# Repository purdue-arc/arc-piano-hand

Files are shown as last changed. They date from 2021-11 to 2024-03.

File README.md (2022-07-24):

---
title: Piano Hand - Overview
date: 2020-09-28 00:00:00 Z
author: Revanth Senthil
---

# Piano Hand - Purdue ARC

## Goal

<u>

### Mission

</u>

The primary objective of Piano Hand is to explore the perspective of robotics in replicating human-motion. Fascination for this included looking at tasks that would help us understand biomechanics, which is an area of robotics that has gained a lot of traction recently. 

The goal of the project is to build a fully autonomous robot arm that can play the piano. The human hand, with 27 degrees of freedom (DOF), has so far been the most dextrous mechanism to play the piano and the closer we get to replicating that degree of freedom and movement, the better it is to move the arm and play the piano.

{% include googleDrivePlayer.html id="1P8rwWDJa1Yuv88X697RMvEq04j1IgpqW/preview" %}

This semester (Fall 2022), we are planning to refine our working model of the animatronic hand built last semester with the help of accurate servo motor and flex sensor functioning. We would expect to extend functioning to two hands as well. Additionally, we are starting a new path in software along the lines of machine learning and optical image recognition by building a model that can read sheet music, given an image format.

---

## Repository Guide

The `Code` directory of this repository contains the software team's work in this project, and the `Models` directory consists of that of the hardware team. The sub-directories in these are divided based on the semester of progress. If any of the directories are incomplete, they will be updated soon. The `wiki` directory contains pretty much the same content as this file, and will be that you see on the wiki page of this project on the <a href="https://wiki.purduearc.com/">Club's Wiki</a>.

---

## What we have done

<u>

### Summer 2022

</u>

Ideated and designed new mechanisms for the hand that involves the usage of linear actuators and bevel gears. This design will be assembled and tested in Fall 2022 as a new iteration from the hand design in Spring 2022.

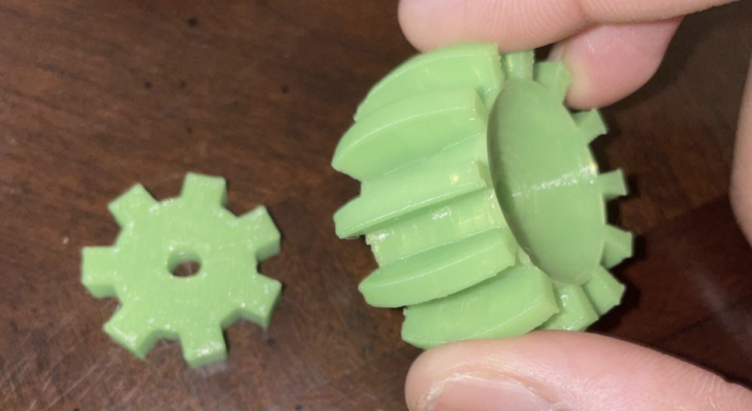
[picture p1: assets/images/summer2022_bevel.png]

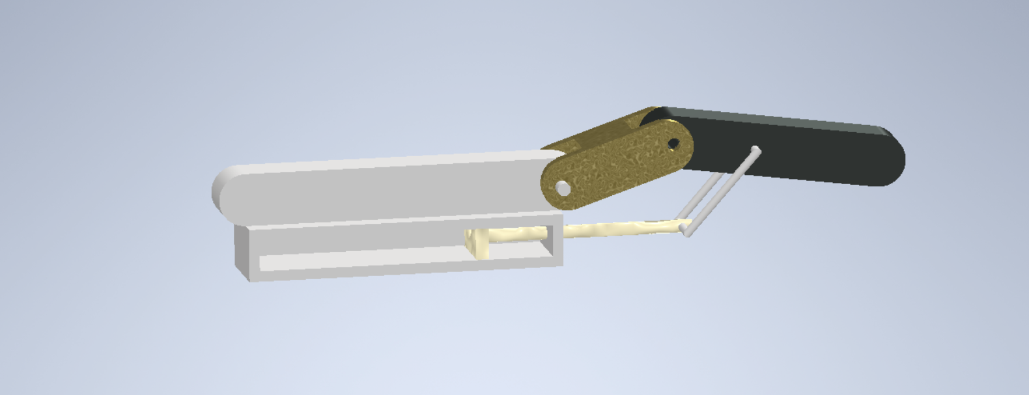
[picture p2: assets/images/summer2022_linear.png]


Worked on fixing issues that came about in software in Spring 2022, and in getting ready the design to implement on the hand in Fall 2023. Introduced new course of action alongside software to start with machine learning and model development in Optical Music Recognition.

Clip from working of servos:

{% include googleDrivePlayer.html id="12XIlDrckEdbvJNI8A9Jp3um2TsCtu46J/view" %}

<u>

### Spring 2022

</u>

Spring2022_Design

Worked on improving model developed in Fall 2021 by printing and testing. An add-on for attaching the servo motors was developed and the design was 3D-printed.

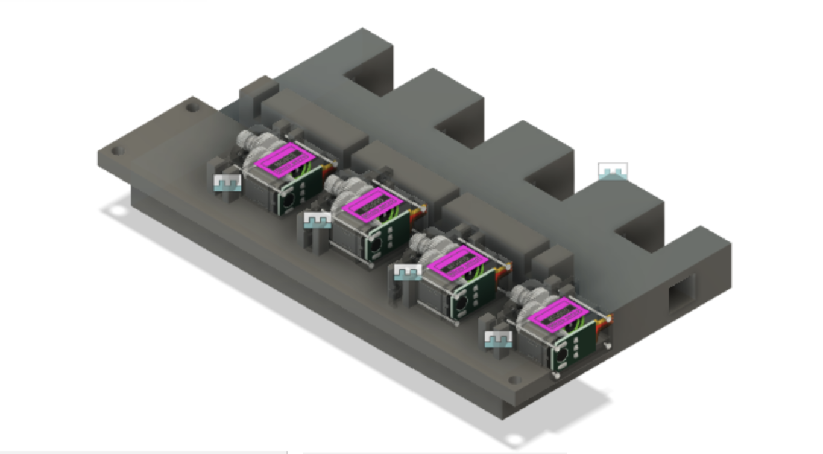
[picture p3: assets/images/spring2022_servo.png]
Spring2022_ServoAttach


Software work primarily included setup of environment on Arudino/Raspberry Pi, along with flex sensors. Issues with the usage of continuous servos were addressed. 8-bit ADCs were also used to improve testing.

{% include googleDrivePlayer.html id="1XUN3-VXOXNSEd7ECZbARMhXspTH0es3h/view" %}

<u>

### Fall 2021

</u>

Worked primarily on developing models and getting an idea of the different parts necessary to 3-D print. Produced the following first iteration of the hand by the end of the semester from hardware.

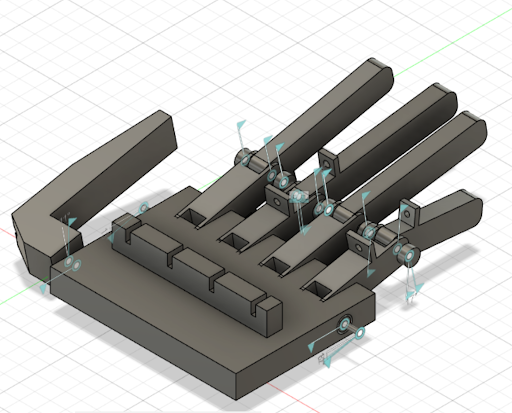
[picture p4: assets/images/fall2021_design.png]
Fall2021_Design


Software primarily worked on simulation and testing, and the following simulation was produced on TinkerCAD (TinkerCAD's electronic component simulator had Arduino testing capabilities and hence was useful for the first stage of testing). TInkerCAD's use-cases for simulation testing were visible from early testing with the software for multiple fingers, using MG90S servos.

{% include googleDrivePlayer.html id="1FLBJuV58_8QRsNKVJZqaC88cPaUbHi6O/view" %}

---

### Subteams and Roster

<u>

#### Project Manager

</u>

Revanth Krishna Senthilkumaran, Computer Engineering

<u>

#### Hardware

</u>

Hardware primarily works on making and refining CAD models with tools available, 3D printing models, assembling, testing and identifying points of improvement in the model and testing functionality. 

<ul>
<li>
<b>Lead</b>: Rugved Dikay, Aeronautical and Aerospace Engineering
</li>
<li>
Akshay, Electrical Engineering
</li>
<li>
Archis Behere, Mechanical Engineering
</li>
</ul>

<u>

#### Software

</u>

Software primarily works on developing the code and algorithms for the movement of the hand to locations computed, along with setup of the electrical systems. More recent initiatives include model development for optical music recognition and Raspberry Pi conversion from Arduino.

<ul>
<li>
Dhruv Sujatha, Data Science
</li>
<li>
Jacob Aldridge, Computer Science
</li>
<li>
Manas Paranjape, Computer Science
</li>
<li>
Visuwanaath Selvam, Computer Engineering
</li>
</ul>

---

<!-- ### Images/GIFs -->

<!-- ## Summary -->

## See Also:

<h3> Inspiration / Other Projects </h3>

<ol>

<li>
 A team of researchers attempted replicating the pressure applied in the grasping mechanism and achieved 17 DOF in a 5-finger hand. The actuators used are the most interesting: McKibben Actuators, which move on the basis of difference in Air Pressure. <a href="https://www.sciencedirect.com/science/article/pii/B9780081005743000102"> ScienceDirect article </a> 
</li>

<li>
The ILDA Robot Hand: A 15 DOF, highly tactile robot hand, motion along surface of palm, and stepper motor actuation. Some of its capabilities include crushing cans, delicate grasping, and tactile tasks such as tapping. <a href="https://gizmodo.com/lifelike-robotic-hand-is-a-bit-too-close-to-terminator-1848213189"> Overview and Videos of Functioning </a> |  <a href="https://www.nature.com/articles/s41467-021-27261-0"> Nature article </a>
</li>

<li>
Soft actuated robots - <a href="https://dash.harvard.edu/bitstream/handle/1/25922120/66841469.pdf;sequence=1"> Harvard paper </a> | 
</li>

<li>
WPI - <a href="https://web.wpi.edu/Pubs/E-project/Available/E-project-042919-161531/unrestricted/Piano_Playing_Robotic_Arm_MQP_-_Final.pdf"> MQP
</li>

<li>
Allegro Hand - <a href="http://wiki.ros.org/Robots/AllegroHand">ROS Documentation</a> | <a href="https://www.youtube.com/watch?v=WzJJ4c6AqnE"> MIT Grad Student's Piano Hand</a>
</li>

<li>
Robot Nano Hand - <a href="https://youtu.be/uOeS_jklU2Y">YouTube</a> | <a href="https://robotnanohand.com/"> Site </a> 
</li>

<li>
InMoov Robot Hand - <a href="https://www.thingiverse.com/thing:17773">Parts and Paper Link</a>
</li>

<li>
Other similar project resources: <a href="https://create.arduino.cc/projecthub/laurencemlai/diy-glove-controlled-robotic-hand-ff5d63"> Arduino Project Hub </a> | <a href="https://www.instructables.com/DIY-Robotic-Hand-Controlled-by-a-Glove-and-Arduino/"> Instructables </a>
</li>

<li>
Video Links/Pages referred: <a href="https://www.youtube.com/c/WillCogley">Will Cogley</a> | Automation Robotics' <a href="https://www.youtube.com/channel/UCd0xLOw6No5IAsq3Y2-b0eA">Clone</a>
</li>

</ol>

<h3> References </h3>

<ol>

<li>
Piano Keys Research - <a href="https://music.stackexchange.com/questions/53847/what-are-the-dimensions-of-piano-keys-in-inches"> Dimensions </a>
</li>

<li>
Joint Design - <a href="https://www.youtube.com/watch?v=AJ9zVYQw5XU">Ball and Socket</a> 
</li>

<li>
Optical Music Recognition Datasets - <a href="https://apacha.github.io/OMR-Datasets/"> Apacha Database List </a> | <a href="https://tuggeluk.github.io/deepscores/"> Deepscores </a> | <a href="https://grfia.dlsi.ua.es/primus/"> Primus </a>
</li>

<li>
Raspberry Pi-Arduino Connectivity - <a href="https://www.aranacorp.com/en/communication-between-raspberry-pi-and-arduino-with-i2c/"> AranaCorp </a> | <a href="https://maker.pro/raspberry-pi/tutorial/raspberry-pi-4-gpio-pinout"> Pi4 GPIO </a> 
</li>

<li>
Parts - <a href="https://cdn-learn.adafruit.com/downloads/pdf/adafruit-4-channel-adc-breakouts.pdf">ADCs</a> | Multi-channel Servo Controller (<a href="https://www.adafruit.com/product/2327?gclid=COGwqIfL99ECFYQDaQodjtQPXQ">16</a>, <a href="https://shop.pimoroni.com/products/servo-2040?variant=39800591679571">18</a>) | <a href="https://www.youtube.com/watch?v=2vAoOYF3m8U"> Linear Servo Actuators </a> - <a href="https://www.myminifactory.com/object/3d-print-77542">CAD Files 1</a>, <a href="https://www.thingiverse.com/thing:3170748/files">CAD Files 2</a>
</li>

<li>
Add-ons: Strings/Thread <a href="https://www.amazon.com/Cotton-String-Cooking-Kitchen-Wrapping/dp/B07KVSVTVV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"> 1 </a>, <a href="https://www.amazon.com/gp/product/B01FICZLU8/ref=ewc_pr_img_2?smid=A27A1UMDQYE0QB&th=1"> 2 </a> | <a href="https://www.amazon.com/Winter-Gloves-Men-Women-Waterproof/dp/B09FPS6HHH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"> Gloves </a>
</li>

<li>
DOF Analysis - <a href="https://www.researchgate.net/publication/264907843_Real-time_hand_tracking_for_rehabilitation_and_character_animation"> +Real-time Hand Tracking </a> | <a href="https://support.ptc.com/help/creo/creo_pma/r6.0/usascii/index.html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">Calculator</a> | <a href="https://www.mecharithm.com/degrees-of-freedom-of-a-robot/"> Mecharithm </a> | <a href="https://www.techopedia.com/definition/12702/six-degrees-of-freedom-6dof"> Technopedia </a>
</li>

<li>
Interesting Actuation Methods - <a href="https://www.frontiersin.org/articles/10.3389/frobt.2020.586216/full">Voltage-Controlled Linear Actuation</a>
</li>

</ol>

<!-- ## References -->

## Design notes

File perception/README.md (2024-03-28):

## Installation
* Install Dependencies (cv2, subprocess,skimage,numpy,imutils)
* Update filepaths (lines 204-206 in camScannerAuto.py)
* Run camScannerAuto.py

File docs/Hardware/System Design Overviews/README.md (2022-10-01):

This folder is to be used to store any documentation developed regarding the different actuation systems researched and modeled
during the design process for Piano Hand. Ultimately these documents/report will serve as the foundation for a comprehensive project
report, while currently demonstrating the thoughts behind engineering decisions, and to guide continous hand improvement.

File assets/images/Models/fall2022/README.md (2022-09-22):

This folder contains all the CAD files for the new designs developed for the Piano Hand during the Fall 2022 Academic semester. In total, 2 different prototype hands were developed: 
One uses geared finger actuation and geared finger seperation, and the other uses linear actuators for actuation, along with a similar geared finger seperation.

All these CAD files have been uploaded in their .f3d formats, or that naturally compatible with Fusion 360 software for easy download and upload. STL conversions
will be provided towards the end of the semester for more general use.

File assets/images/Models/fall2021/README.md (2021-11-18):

# CAD Models for the Piano Hand

### Hardware team of Piano Hand to upload CAD Models of the Hand and its progress throughout the semester, including the ProtoHand

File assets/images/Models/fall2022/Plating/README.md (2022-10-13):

This folder will serve as a repository for all CAD files related to supporting elements of the Piano Hand design. Primarily this refers to the plating that shall
surround the different components, gears, and joints of the hand as well as any connecting parts between these plates and the internal elements.

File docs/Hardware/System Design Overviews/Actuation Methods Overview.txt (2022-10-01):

After reviewing different finger actuation systems such as using gears, cables, and linear actuators as well as creating a prototype based on the cable method last semester, linear actuation will be the focus this semester. The cable based method turned out to be unreliable to control and code for finer motion. Due to the results from testing the cable method, linear actuators seem to be a better alternative both in regards to precision and most imporantly in size. Though right now the focus is on linear actuators, gear-based systems are also one alternative we are considering possibly in combination to linear actuators.

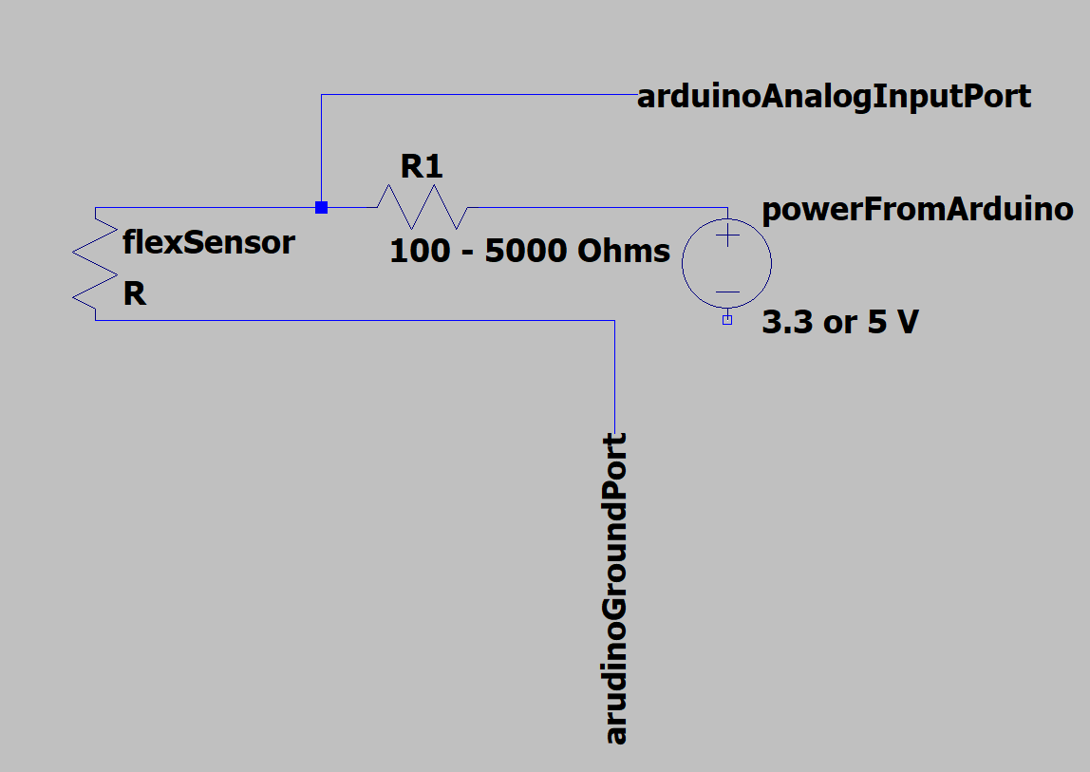
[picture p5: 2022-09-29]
src/code_timeline/fall2022/flexSensorCircuit.png

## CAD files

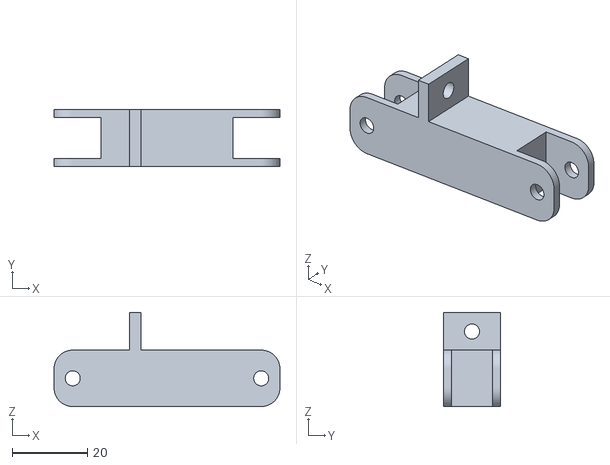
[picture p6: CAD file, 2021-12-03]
assets/images/Models/fall2021/Main_Finger_Joint.stl
60.0 x 15.0 x 25.0

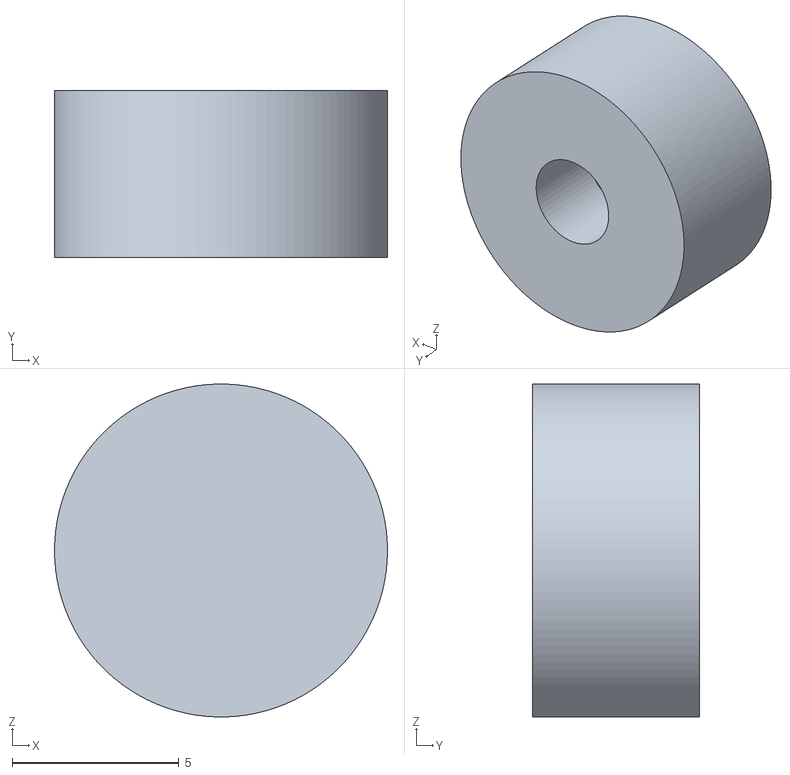
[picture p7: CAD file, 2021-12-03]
assets/images/Models/fall2021/Rod_Caps.stl
10.0 x 5.00 x 10.00

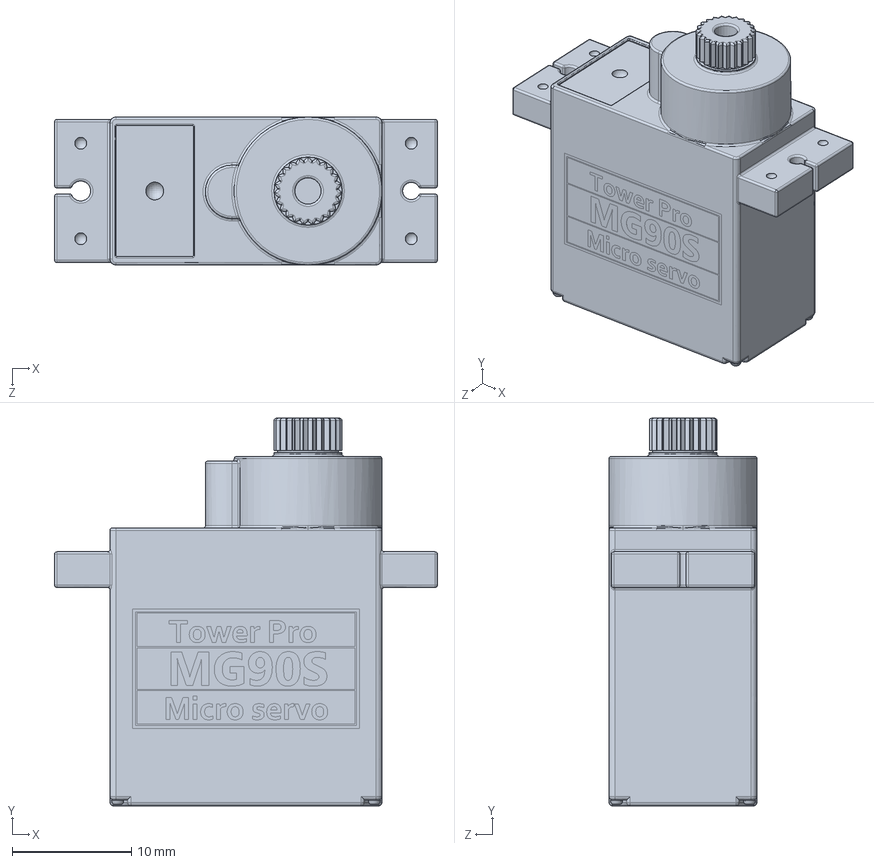
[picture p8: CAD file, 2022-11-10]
assets/images/Models/fall2022/Tower-Pro-MG90S.SLDPRT
32.1 x 32.5 x 12.4 mm

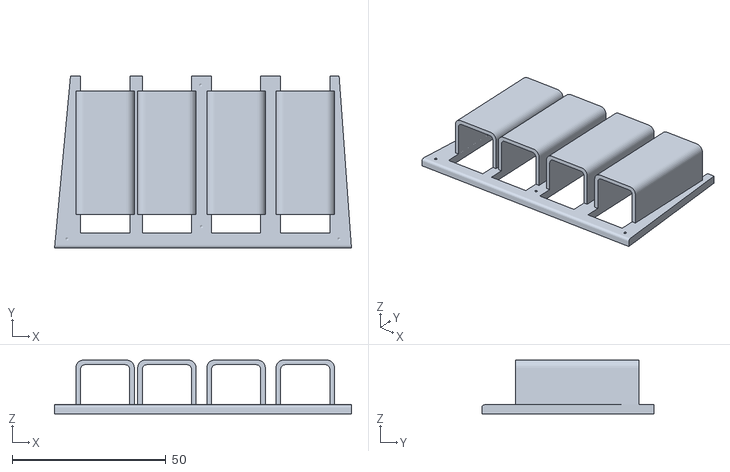
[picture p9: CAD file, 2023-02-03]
assets/images/Models/spring2023/Actuator Securing Plate v1 v3.stl
96.5 x 56.0 x 17.5

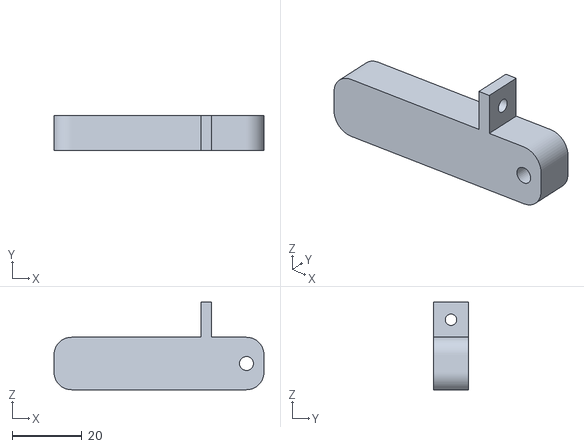
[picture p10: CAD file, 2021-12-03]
assets/images/Models/fall2021/Pinky_Finger_Design.stl
60.0 x 10.0 x 25.0

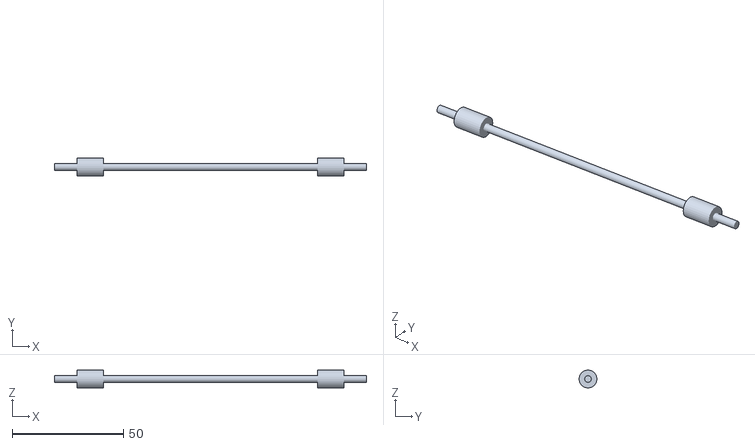
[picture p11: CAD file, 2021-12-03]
assets/images/Models/fall2021/Connecting Rod_Hand.stl
140.0 x 8.00 x 7.96

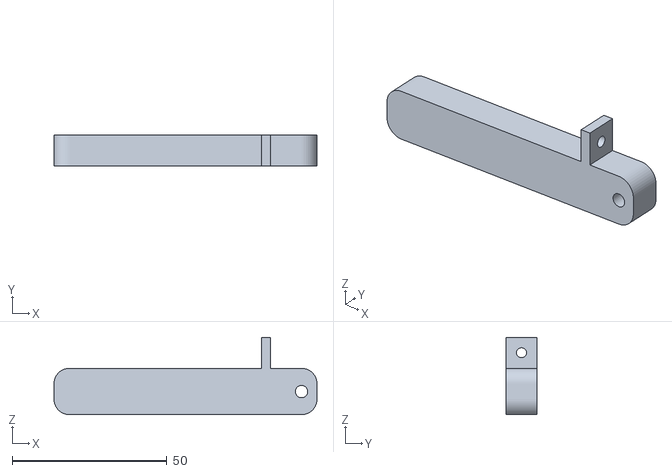
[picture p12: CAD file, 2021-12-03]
assets/images/Models/fall2021/Index_Finger_Design.stl
85.0 x 10.0 x 25.0

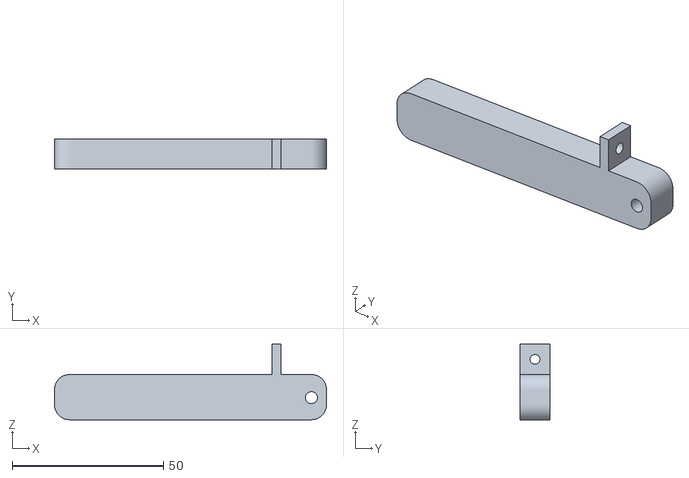
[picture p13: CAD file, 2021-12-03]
assets/images/Models/fall2021/Ring_Finger_Design.stl
90.0 x 10.0 x 25.0

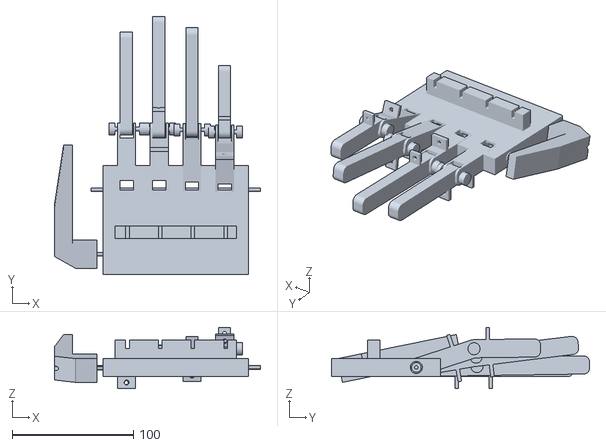
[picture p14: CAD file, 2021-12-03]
assets/images/Models/fall2021/Palm_Design.stl
170.0 x 213.3 x 50.6

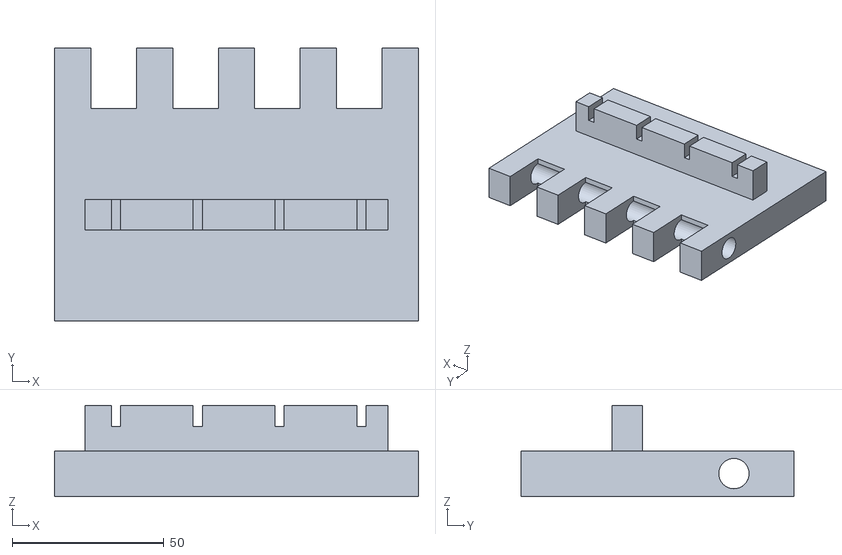
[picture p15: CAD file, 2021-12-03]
assets/images/Models/fall2021/Protohand palm v3.stl
120.0 x 90.0 x 30.0

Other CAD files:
src/code_timeline/fall2023/Algos-code/main.obj
src/code_timeline/fall2023/Algos-code/Trellis.obj
src/code_timeline/fall2023/Algos-code/Finger.obj
src/code_timeline/fall2023/Algos-code/Hand.obj
src/code_timeline/fall2023/Algos-code/FingerStateAllocationAlgorithm.obj
src/code_timeline/fall2023/Algos-code/Viterbi.obj
src/code_timeline/fall2023/Algos-code/Note.obj
src/code_timeline/fall2023/Algos-code/Layer.obj
assets/images/Models/fall2021/Connecting_Rod_Finger_Joint.stl
assets/images/Models/fall2021/Hand_Assembly.f3z
assets/images/Models/fall2021/Middle_Finger_Jointed v6.f3z
assets/images/Models/fall2021/Middle_Finger_Jointed.stl
assets/images/Models/fall2021/Protohand palm v3 (1).f3d
assets/images/Models/fall2021/Protohand palm v3.f3d
assets/images/Models/fall2021/Protohand palm v3new.f3d
assets/images/Models/fall2021/Thumb_Initial_Design.stl
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

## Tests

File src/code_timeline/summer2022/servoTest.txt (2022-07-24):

myservo.write(val):

val == 0        : max clockwise
0 < val < 90    : clockwise 
val == 90       : stop
90 < val < 180  : anti-clockwise
val == 180      : max anti-clockwise

max servo speed     : 0.11s / 60 deg
min servo speed     : 0.08s / 60 deg

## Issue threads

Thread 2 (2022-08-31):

Finding Suitable Datasets to work with

revanthsenthil, 2022-08-31:
Finding optical music recognition datasets to work with to get started on that track.

revanthsenthil, 2022-08-31:
It has been noted with communication with the software team that suitable datasets don't exist for this project and they are to be made from scratch by the team. We will initiate a new course of action to start making datasets just in case.

revanthsenthil, 2022-09-22:
music21 has been found to be the way to go at the moment, so I will close this issue and create a new one to work with the music21 dataset.

Closed 2022-09-22.

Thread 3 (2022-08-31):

Develop working code for 5 fingers

revanthsenthil, 2022-08-31:
Using the code developed for two flex sensors and servos to 5 fingers (5 servos and flex sensors) so it becomes more applicable for one hand.

Code developed:

```
#include <Servo.h>

#define SERV_CCW(SC) (90 + ((SC) / 3))
#define SERV_CW(SC) (90 - ((SC) / 3))
#define SERV_STILL 90

#define ANGLE_THRESH 5
#define CW_TEST 60
#define CCW_TEST 120
#define SERVO_DELAY 200

Servo ph_servo0;
Servo ph_servo1;

float x, x2;
int angle, angle2;
int prev_angle = 1000;  // some random high value
int prev_angle2 = 1000;
int servo_set;

int servo_val(float analog_val);
void servo_pos(int angle, int prev_angle);

void setup()
{
  pinMode(13, OUTPUT);
  pinMode(A0, INPUT);
  pinMode(A1, INPUT);
  ph_servo0.attach(9);
  ph_servo1.attach(8);
  Serial.begin(9600);
}

void loop()
{
  //ph_servo0.write(130);

  x = analogRead(A0);
  x2 = analogRead(A1);
  angle = servo_val(x);
  angle2 = servo_val(x2);

  // if (prev_angle != 1000) {
  Serial.print("1: ");
  Serial.print(angle);
  Serial.print(", 2: ");
  Serial.println(angle2);

  //   servo_pos(angle, prev_angle);

  //   ph_servo0.write(servo_set);
  // }

  if (angle > prev_angle + 5) {
    ph_servo0.write(CCW_TEST);
  } else if (angle < prev_angle - 5) {
    ph_servo0.write(CW_TEST);
  } else {
    ph_servo0.write(SERV_STILL);
  }

  if (angle2 > prev_angle2 + 5) {
    ph_servo1.write(CCW_TEST);
  } else if (angle2 < prev_angle2 - 5) {
    ph_servo1.write(CW_TEST);
  } else {
    ph_servo1.write(SERV_STILL);
  }

  prev_angle = angle;
  prev_angle2 = angle2;
  delay(SERVO_DELAY);
  // delay(100); // to include a buffer between two different readings

}

int servo_val(float analog_val) {
  // calculates the angle from one of the methods discussed in #general
  float c_analogVal = ((analog_val - 159) / 352);
  int angle = (c_analogVal * 180);
  return angle;
}
```

revanthsenthil, 2023-01-27:
This issue converted to a different approach. Hence, will be closed as not planned

Closed 2023-01-27.

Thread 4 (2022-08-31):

Fixing Servo code for continuous servos

revanthsenthil, 2022-08-31:
### Final Summer Iteration
```
#include <Servo.h>

#define SERV_CCW(SC) (90 + ((SC) / 3))
#define SERV_CW(SC) (90 - ((SC) / 3))
#define SERV_STILL 90

#define ANGLE_THRESH 5
#define CW_TEST 60
#define CCW_TEST 120
#define SERVO_DELAY 200

Servo ph_servo0;
Servo ph_servo1;

float x, x2;
int angle, angle2;
int prev_angle = 1000;  // some random high value
int prev_angle2 = 1000;
int servo_set;

int servo_val(float analog_val);
void servo_pos(int angle, int prev_angle);

void setup()
{
  pinMode(13, OUTPUT);
  pinMode(A0, INPUT);
  pinMode(A1, INPUT);
  ph_servo0.attach(9);
  ph_servo1.attach(8);
  Serial.begin(9600);
}

void loop()
{
  //ph_servo0.write(130);

  x = analogRead(A0);
  x2 = analogRead(A1);
  angle = servo_val(x);
  angle2 = servo_val(x2);

  // if (prev_angle != 1000) {
  Serial.print("1: ");
  Serial.print(angle);
  Serial.print(", 2: ");
  Serial.println(angle2);

  //   servo_pos(angle, prev_angle);

  //   ph_servo0.write(servo_set);
  // }

  if (angle > prev_angle + 5) {
    ph_servo0.write(CCW_TEST);
  } else if (angle < prev_angle - 5) {
    ph_servo0.write(CW_TEST);
  } else {
    ph_servo0.write(SERV_STILL);
  }

  if (angle2 > prev_angle2 + 5) {
    ph_servo1.write(CCW_TEST);
  } else if (angle2 < prev_angle2 - 5) {
    ph_servo1.write(CW_TEST);
  } else {
    ph_servo1.write(SERV_STILL);
  }

  prev_angle = angle;
  prev_angle2 = angle2;
  delay(SERVO_DELAY);
  // delay(100); // to include a buffer between two different readings

}

int servo_val(float analog_val) {
  // calculates the angle from one of the methods discussed in #general
  float c_analogVal = ((analog_val - 159) / 352);
  int angle = (c_analogVal * 180);
  return angle;
}
```

The `servo_pos` function:
```
void servo_pos(int angle, int prev_angle) {
  // anti-clockwise = down == angle < prev_angle

  if (angle > prev_angle) {
    ph_servo0.write(120);
  } else if (angle < prev_angle) {
    ph_servo0.write(60);
  } else {
    ph_servo0.write(SERV_STILL);
  }

}
```
---

### Iteration 1:

```
#include <Servo.h>

#define SERV_CCW(SC) (90 + ((SC) / 3))
#define SERV_CW(SC) (90 - ((SC) / 3))
#define SERV_STILL 0

Servo ph_servo0;

int angle;
int prev_angle = 1000;
int servo_set;

int servo_val(float analog_val);
void servo_pos(int angle, int prev_angle);

void setup()
{
  pinMode(13, OUTPUT);
  pinMode(A0, INPUT);
  ph_servo0.attach(9);
  Serial.begin(9600);
}

void loop()
{
  //ph_servo0.write(130);

  float x = analogRead(A0);
  angle = servo_val(x);

  if (prev_angle != 1000) {
    Serial.println(angle);
    servo_pos(angle, prev_angle);

    ph_servo0.write(servo_set);
  }

  prev_angle = angle;
  // delay(100); // to include a buffer between two different readings

}

int servo_val(float analog_val) {
  // calculates the angle from one of the methods discussed in #general
  float c_analogVal = ((analog_val - 159) / 352);
  int angle = (c_analogVal * 180);
  return angle;
}

void servo_pos(int angle, int prev_angle) {
  // anti-clockwise = down == angle < prev_angle

  if (angle > prev_angle) {
    ph_servo0.write(SERV_CCW(prev_angle - angle));
  } else if (angle < prev_angle) {
    ph_servo0.write(SERV_CW(prev_angle - angle));
  } else {
    ph_servo0.write(SERV_STILL);
  }

}
```

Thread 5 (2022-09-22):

Create code to read, transmit, save, and display data from the flex sensor glove

Visuwanaath, 2022-09-22:

Closed 2023-01-27.

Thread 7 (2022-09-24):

Piano Hand Hardware Design Review

Rugved-Dikay, 2022-09-24:
A formal report of all hardware design progress and ideation for the Piano Hand.

Rugved-Dikay, 2022-09-24:
To start off this semester, me and Revanth have decided to start the development of a hardware design review document/report. In general, this report will be a compilation of the design process we have used throughout the semester, any research performed into different systems and processes, and of plans for continuous development and integration of the project. As of right now the structure has yet to be finalized but will be soon, with weekly assignments given to y'all alongside whatever CAD work is needed, such as like writing one to two paragraphs about a new design choice the team made, or actuation research. Ultimately by the end of the sem, we should hopefully have a foundation of an industry standard report for ARC, and all relevant stakeholders, including ourselves, to truly cherish. Thus I wanted to make this project an ongoing issue within GitHub and will soon be making follow-up posts regarding the matter.

Why a paper?

The purpose of this deliverable is to not only create a record of the Piano Hand's progress throughout the upcoming months and semester as a tool for ARC and planning future project work, but mainly to offer all of us a professional document to validate our hard work, and show off to recruiters, companies, and professors alike in the future. Per personal experiences, I can attest to the value of having a paper/report under your name, especially as this early stage in our undergraduate and professional lives, as a tool of distinguishing ourselves from other candidates and demonstrating to engineering and tech firms, how we have already developed a lot of the skills we are looking for: Technical writing, research, systems engineering to name a few. Moreover, this will be a chance for us to communicate the research and knowledge we have gained through this project in a very professional and marketable manner, as yet another edge offered for our career development.

 However, this document will not have the standards needed to offer the many things I have mentioned, unless we all chip in, and so I really hope you all can contribute in some way, beyond the amazing work we will be doing with CAD and actual hardware.

revanthsenthil, 2023-01-27:
Completed at Design Review

Closed 2023-01-27.

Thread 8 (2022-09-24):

MIDI Formatting, Conversion

revanthsenthil, 2022-09-24:

revanthsenthil, 2022-09-24:
List of things currently considered:

- Mido - primary approach to processing MIDI data
- Based on sample conducted with `my_heart_will_go_on1.mid` - channel separation possible, processing of different channels
- @TPNxl has Ableton, so visual processing of Midi data possible

revanthsenthil, 2022-09-29:
MIDI -> Keyboard output and Keyboard to MIDO-convertable MIDI obtianed

revanthsenthil, 2022-09-29:
Completed, will move on to servo interfacing. Mido+MIDI work in progress still.

revanthsenthil, 2023-09-09:
closed due to migration

Closed 2023-09-09.

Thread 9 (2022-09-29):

Interfacing servo with MIDI

revanthsenthil, 2022-09-29:

revanthsenthil, 2022-10-01:
State Generation:

considered:
 - Creating API to interface MIDI with Arduino
 - Arduino code for controlling actuators
 - Performing a level of computation on the arduino

primary iteration:
 - using I2C ports on arduino to send information,
 - no arduino code from ph-software-junction really necessary, but serial comm

revanthsenthil, 2023-09-09:
closed due to migration

Closed 2023-09-09.

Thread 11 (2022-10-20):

Setting up Sim for Piano Hand

revanthsenthil, 2022-10-20:
Finding a suitable simulation environment and deploying models onto simulation for testing.

revanthsenthil, 2022-10-22:
Using Unity for Sim

revanthsenthil, 2023-01-27:
Currently setting up and understanding webots for all members

NarenR21, 2023-02-03:
Goals and Timeline for Sim: (Individual task will be detailed below.)

Feb 11th finalize familiarity and training.
Feb 18th able to read a force sensor on the fingertip
Mar 2nd simple algorithm

Closed 2023-09-09.

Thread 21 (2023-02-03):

Write simple fingering enumeration algorithm

TPNxl, 2023-02-03:
We need to write an algorithm that enumerates fingering states for a given set of notes.

**Input:** An array of type Note[] containing all the notes being played at a given time

**Output:** A array of type FingeringState[] containing all the possible fingering states for the given set of notes.

**Current constraints:**

- The hand cannot move.
- Fingers cannot cross over one another.

**Specifics:**

- Returns an error if the notes cannot be played with the given constraints

TPNxl, 2023-02-03:
https://docs.google.com/document/d/1gBkU89XLWgaahsnRjlPmHvMwvkgi4K4KTkR29OqLoHo/edit

Closed 2023-09-09.

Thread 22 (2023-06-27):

Summer 2023 Plan

revanthsenthil, 2023-06-27:
# Plan for Meetings: Summer 2023 (and changes)

## Biggest Task for Everyone: **_Complete Documentation_**

- Long awaited, must do before BGR week (Incoming Freshmen should be able to view docs during B-Involved fair)
- Me: refork the ARC wiki git repo, start edits for each sub-team and format
- Everyone on Piano Hand: Edit respective parts as I do them too

### Progress updates will be from now on in the form of slides - I will make a slide deck that we update every 4 weeks with progress updates throughout the semester. (Starting Fall 2023)

# Sub-team Specific Tasks:

## Hardware

Design ideation and modelling for wrist motion, increasing finger-DOF motion and for along the piano (rails/joints, etc.)

## Software

### Electronics + Junction

- Simple PCB setup and ordering, getting a simulated version of control setup, more diagrams of current system and future implementations
- Getting team familiar with PCB Design and modeling
- Also ordering a simple PCB from a site to test it out
- Solid JSON format + playing on simulation (work with Sim sub-team)

### Algorithms

- Develop a concrete idea of states and progressing forward with it with one unified language setup
- Full understanding of git branches, and GH usage, especially considering you are the only core-software team

### Sim + Data

- Get simulation of one hand playing music working
- Making sim more modular with code, so any new hardware model can be imported and implemented
- Understanding of CNN and progression with model

revanthsenthil, 2023-09-09:
closed due to migration

Closed 2023-09-09.

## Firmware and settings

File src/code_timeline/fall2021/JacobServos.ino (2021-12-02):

#include <Servo.h>

Servo pinkyServo;
Servo ringServo;
Servo middleServo;
Servo pointerServo;
Servo thumbServo;
Servo wristServo;

int thumbAngle = 0;
int pointerAngle = 0;
int middleAngle = 0;
int ringAngle = 0;
int pinkyAngle = 0;

int wristAngleOffset = 0;
const int defaultWristAngle = 90;
const int pressKeyAngle = 30;
String keys[] = {"C3","C#","D","D#","E","F","F#","G","G#","A","A#","B","C4"};
void setup() {
  pinkyServo.attach(3);
  ringServo.attach(5);
  middleServo.attach(6);
  pointerServo.attach(9);
  thumbServo.attach(10);
  wristServo.attach(11); 
    
  Serial.begin(9600);
  
  pinkyServo.write(0);
  ringServo.write(0);
  middleServo.write(0);
  pointerServo.write(0);
  thumbServo.write(0);
  wristServo.write(defaultWristAngle);
  delay(1000);
}

void loop() {
    //Takes input from the serial and then plays the specified key
    while(Serial.available() > 0 ){
        String str = Serial.readString();
        for(int i = 0;i < 13;i++){
            if(str.indexOf(keys[i]) > -1){
                playKey(str);
                break;
            }else{
                Serial.println("Invalid Key");
            }
        }
    }
}

// Plays the given key and goes back to default pos
void playKey(String key) {
  setAngles(key);
  moveServos();
  resetFingerJoints();
}

// Sets finger/wrist angle based on key pressed
// Note: must distinguish between C3 and C4
// Note: accidentals are always sharp
void setAngles(String key) {
  if (key.equals("C3")) {
    wristAngleOffset = 0;
    thumbAngle = pressKeyAngle;
    
  } else if (key.equals("C#")) {
    wristAngleOffset = 15;
    pointerAngle = pressKeyAngle;
    
  } else if (key.equals("D")) {
    wristAngleOffset = 7;
    pointerAngle = pressKeyAngle;
    
  } else if (key.equals("D#")) {
    wristAngleOffset = 0;
    pointerAngle = pressKeyAngle;
    
  } else if (key.equals("E")) {
    wristAngleOffset = 3;
    middleAngle = pressKeyAngle;
    
  } else if (key.equals("F")) {
    wristAngleOffset = 0;
    middleAngle = pressKeyAngle;
    
  } else if (key.equals("F#")) {
    wristAngleOffset = -5;
    middleAngle = pressKeyAngle;
    
  } else if (key.equals("G")) {
    wristAngleOffset = 0;
    ringAngle = pressKeyAngle;
    
  } else if (key.equals("G#")) {
    wristAngleOffset = -3;
    ringAngle = pressKeyAngle;
    
  } else if (key.equals("A")) {
    wristAngleOffset = 0;
    pinkyAngle = pressKeyAngle;
    
  } else if (key.equals("A#")) {
    wristAngleOffset = -5;
    pinkyAngle = pressKeyAngle;
    
  } else if (key.equals("B")) {
    wristAngleOffset = -8;
    pinkyAngle = pressKeyAngle;
    
  } else if (key.equals("C4")) {
    wristAngleOffset = -12;
    pinkyAngle = pressKeyAngle;
  }
  
}

// Gives time for the finger and wrist to move
void moveServos() {
  setFingerJoints();
  wristServo.write(defaultWristAngle + wristAngleOffset);
  delay(300);
}

// Gives time for the fingers to return to normal pos
void resetFingerJoints() {
  thumbAngle = 0;
  pointerAngle = 0;
  middleAngle = 0;
  ringAngle = 0;
  pinkyAngle = 0;
  setFingerJoints();
  delay(250); 
}

void setFingerJoints() {
  thumbServo.write(thumbAngle);
  pointerServo.write(pointerAngle);
  middleServo.write(middleAngle);
  ringServo.write(ringAngle);
  pinkyServo.write(pinkyAngle);
}

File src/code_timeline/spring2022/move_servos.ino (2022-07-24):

#include <servo.h>

Servo servo0;
Servo servo1;
Servo servo2;
Servo servo3;
Servo servo4;

int pin0 = 0;
int pin1 = 1;
int pin2 = 2;
int pin3 = 3;
int pin4 = 4;

void setup() {
  // put your setup code here, to run once:
  Serial.begin(9600);

  servo0.attach(pin0);
  servo0.attach(pin1);
  servo0.attach(pin2);
  servo0.attach(pin3);
  servo0.attach(pin4);

  servo0.write(90);
  servo1.write(90);
  servo2.write(90);
  servo3.write(90);
  servo4.write(90);
}

void loop() {
  // put your main code here, to run repeatedly:
  servo0.write(180);
  servo1.write(180);
  servo2.write(180);
  servo3.write(180);
  servo4.write(180);

  delay(500);

  servo0.write(90);
  servo1.write(90);
  servo2.write(90);
  servo3.write(90);
  servo4.write(90);

  delay(500);
  
  servo0.write(0);
  servo1.write(0);
  servo2.write(0);
  servo3.write(0);
  servo4.write(0);

  delay(500);
  
  servo0.write(90);
  servo1.write(90);
  servo2.write(90);
  servo3.write(90);
  servo4.write(90);

  delay(500);
}

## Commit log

2021-11-21 Added my Servo Code
2021-12-02 Added function for setting finger position
2021-12-03 add prototype 1 files via upload
    [Connecting Rod_Hand.stl, Connecting_Rod_Finger_Joint.stl, Index_Finger_Design.stl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]
2022-07-24 changes made to repo structure
    [Connecting Rod_Hand.stl, Connecting_Rod_Finger_Joint.stl, Hand_Assembly.f3z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]
2022-09-24 added samples dir
2022-09-24 Please enter the commit message for your changes. Lines starting
    Added new test midi track file and parsing notebook
2022-09-30 Add files via upload
    Top cover for base plate
    [top-plate v1.f3d]
2022-10-01 Add files via upload
    Base plate file with holes added for gears
    [base-plate v2 v1.f3d]
2022-10-13 Added a rudimentary algorithm to allocate fingers to fingerMethods.py
2022-10-20 PySerial and ArduinoJSON parsing and communication demo
2022-10-27 Add files via upload
    Current assembly of the piano hand design. Note that a lot more file management would be desirable to organize all the different types of files and components, based on their role/function within the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
    [Current Final Hand Assembly.f3z]
2022-10-27 added a bunch of stuff, two fingers work now
2022-11-05 more than one finger stuff not sure if it works yet
2023-01-29 Add files via upload
    Base plate with indents for Linear actuators
    [base-plate v2 v1 v9.f3d]
2023-01-29 directory reorganization
    [base-plate v2 v1 v9.f3d]
2023-03-20 Added more algorithms code - finished finger state alloc algo
2023-09-01 Fixed some C++ code
    [Finger.obj, FingerStateAllocationAlgorithm.obj, Hand.obj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]
2023-09-16 Get pot vals for 1 finger
2023-09-16 Added getting potentiometer values for one finger
    Computer sends signal to Arduino. Arduino sends back potentiometer values back to computer.
2023-09-26 schematic 1
    [Piano_Hand_1.kicad_sch]
2023-09-30 BANG BANG
    Added the code to move fingers by some angle. More PID stuff needed I guess. Also do not have inputs from computer. However, able to access potentiometer values and get current angles.
    Also need the calculations to convert a potentiometer value to angle.
2023-10-14 Errors are fixed
    So many errors. I did not add any more logic. Still need to receive potentiometer values from Arduino. Also, still need logic calculate voltage to move fingers.
    [Get Pot Vals.ino]
2024-03-03 Create cam.py
    To replace with camera code
2024-03-03 camera2mxl code
2024-03-03 Create README.md
    documentation to run camera to musicxml
